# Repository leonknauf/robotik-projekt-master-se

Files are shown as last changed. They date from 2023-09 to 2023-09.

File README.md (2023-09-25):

# D.E.E.Z. N.U.T.S.
**Dynamic Eatables Emitting Zone - Nut Utility Transportation System**

Hier sind alle Projektinformationen sowie die Software für das N.U.T.S Projekt im Rahmen des Moduls Projekt Robotik im Studiengang Systems Engineering von StudiumPlus zu finden.
Anbei einige Bilder, die das Projektergebnis festhalten.
Unter [Releases](https://github.com/leonknauf/robotik-projekt-master-se/releases/tag/release) findet sich außerdem die Präsentation und Dokumentation des Projekt, sowie ein kurzes Werbevideo zu unserem Konzept.

Falls in Zukunft an diesem Projekt weitergearbeitet wird, stehe ich zu Fragen zu dem Projekt oder speziell zu der Software zu Verfügung.

~ Leon Knauf

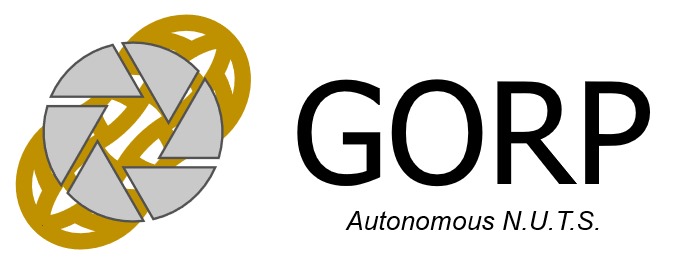
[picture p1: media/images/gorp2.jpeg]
GORP

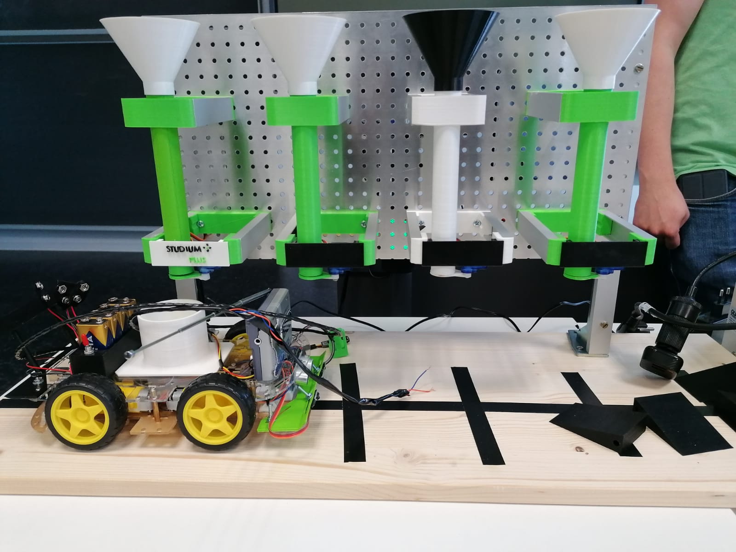
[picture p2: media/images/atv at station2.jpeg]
Vehicle at Station

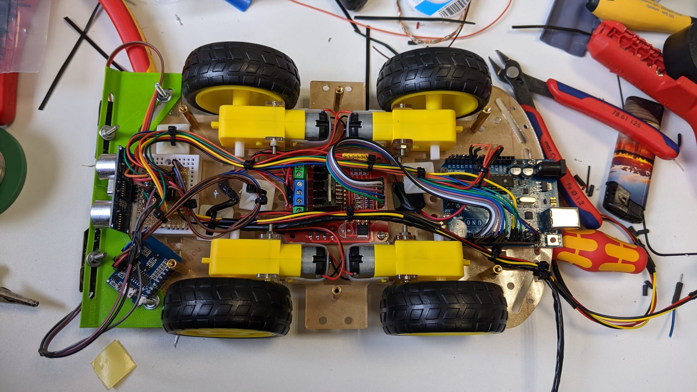
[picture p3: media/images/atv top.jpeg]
Vehicle

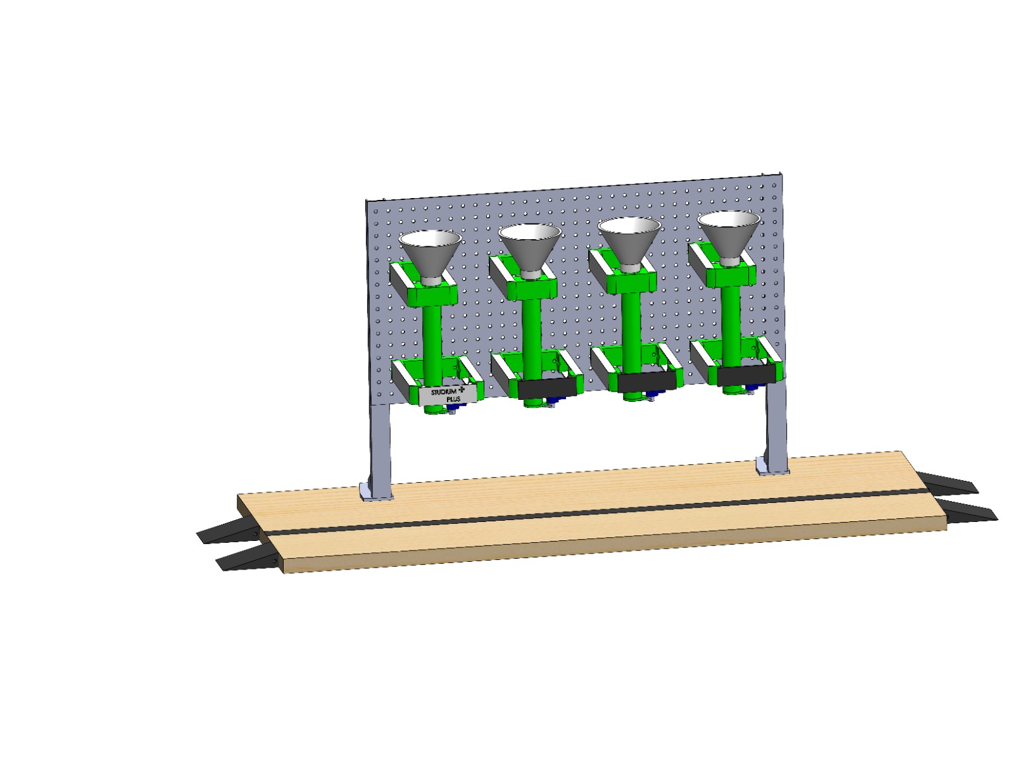
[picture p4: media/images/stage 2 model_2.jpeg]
Station

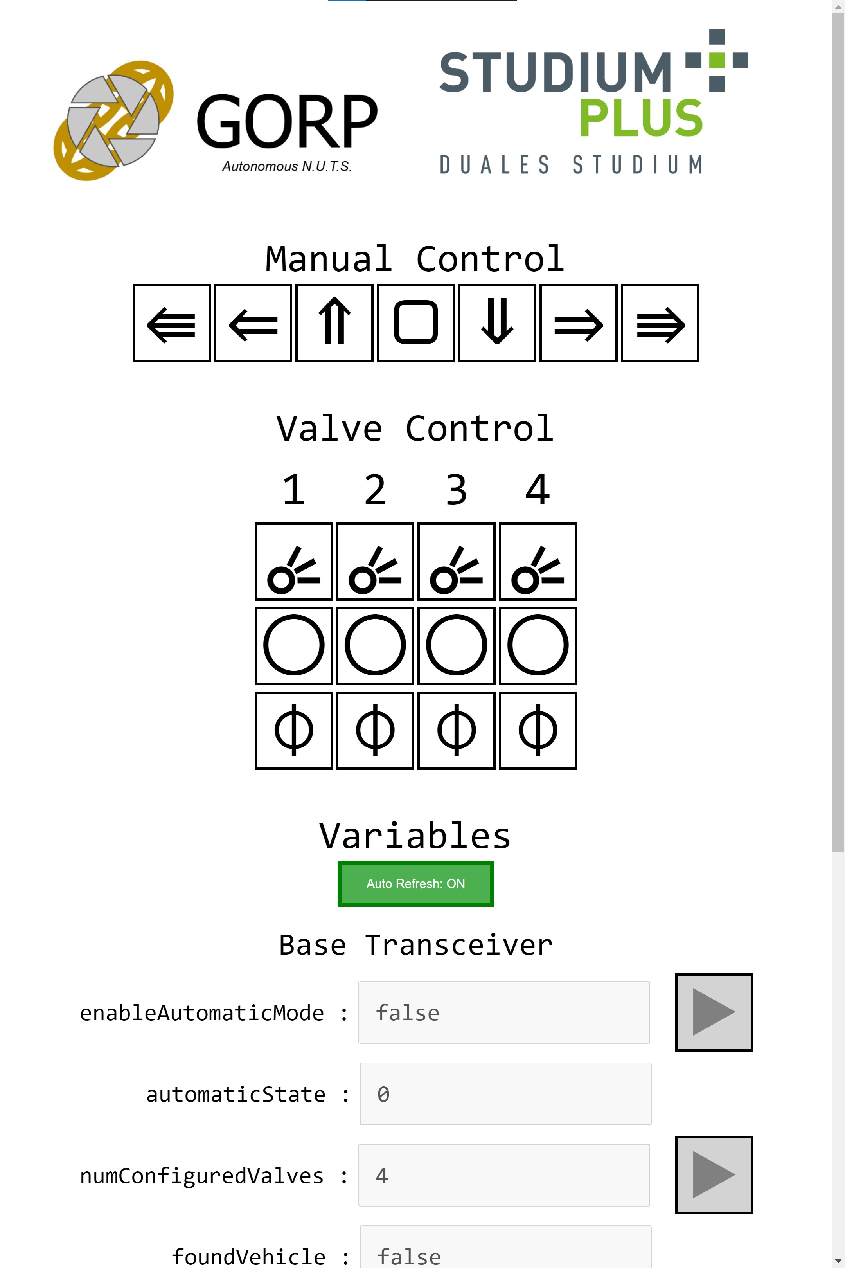
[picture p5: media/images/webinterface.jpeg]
Webinterface


SIEBEL!!!

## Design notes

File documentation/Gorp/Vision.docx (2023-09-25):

# Vision

# Mission Statement

Wir wollen eine Studentenfuttermischmaschine bauen.

Es sollen rohe Nüsse eingefügt und geknackt werden.

Die geknackten Nüsse sollen zusammen mit getrocknetem Obst in eine Tüte verpackt werden.

Optional soll ein AGV die Tüte weitertransportieren.

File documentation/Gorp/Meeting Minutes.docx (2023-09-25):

# Meeting Minutes

# 07.07.2023

- Brainstorming welche Projekte
  - Hauptfokus Nussknacker / Studentenfuttermischmaschine
  - Optional: AGV mit Computer Vision & Path Planning
- Nussknacker
  - Schwungrad, Feder, Rohr
  - hygienisch → Edelstahl

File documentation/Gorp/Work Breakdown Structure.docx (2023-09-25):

# Work Breakdown Structure

- Project Management Activities
  - Process Documentation Activities
    - Setup Communication Channel
      - State: Done
      - Priority: High
      - Assignee: Marvin Müller
      - Planned For: 07.07.2023
      - Completion Date: 07.07.2023
      - Comment: WhatsApp Group set up
    - Setup Documentation Channel
      - State: Done
      - Priority: High
      - Assignee: Marvin Müller
      - Planned For: CW31
      - Completion Date: 04.08.2023
      - Comment: Google Drive folder set up, following documents provided: Vision, Project Plan, Requirement Specification, Test Spec Report, Work Breakdown Structure / Kanban, Meeting Minutes
  - Work Planning Activities
    - Review Meeting with Team Members
      - State: Open
      - Priority: High
      - Assignee:
      - Planned For:
      - Completion Date:
      - Comment:
- Development Activities
  - Mechanical Development Activities
    - Identify Mechanical Components
      - State: Open
      - Priority: High
      - Assignee:
      - Planned For:
      - Completion Date:
      - Comment:
    - Order Mechanical Components
      - State: Open
      - Priority: High
      - Assignee:
      - Planned For:
      - Completion Date:
      - Comment:
    - Assemble Mechanical Components
      - State: Open
      - Priority: High
      - Assignee:
      - Planned For:
      - Completion Date:
      - Comment:
  - Electrical Development Activities
    - Provide Power Supply
      - State: Open
      - Priority: High
      - Assignee:
      - Planned For:
      - Completion Date:
      - Comment:
    - Create AGV
      - State: Open
      - Priority: Low
      - Assignee:
      - Planned For:
      - Completion Date:
      - Comment:
- Test Activities
  - Mechanical Test Activities
    - Nutcracking Tests
      - State: Open
      - Priority: High
      - Assignee:
      - Planned For:
      - Completion Date:
      - Comment:
    - Nutshell Removal Tests
      - State: Open
      - Priority: High
      - Assignee:
      - Planned For:
      - Completion Date:
      - Comment:
  - Electrical Test Activities
    - Power Supply Test
      - State: Open
      - Priority: High
      - Assignee:
      - Planned For:
      - Completion Date:
      - Comment:
    - AGV Test
      - State: Open
      - Priority: Low
      - Assignee:
      - Planned For:
      - Completion Date:
      - Comment:

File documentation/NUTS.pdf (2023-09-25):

Projektbeschreibung Autonomous N.U.T.S | Gorp Group
SE Robotik-Projekt SS23 | Dipl-.Ing. F. Wasinski, Prof. Dr.-Ing. W. Bonath

Projektbeschreibung Autonomous N.U.T.S.

Eingereicht: 24.09.2023

## Inhalt

## Abbildungsverzeichnis

Abb. 1: Gesamtübersicht initiale Planung des N.U.T.S | 4
Abb. 2: High-Level Architektur von Stufe 2 | 5
Abb. 3: Detailed-Level Architektur von Stufe 2 | 5
Abb. 4: High-Level Architektur von Stufe 3 | 6
Abb. 5: Detailed-Level Architektur von Stufe 3 | 6
Abb. 6: High-Level Architektur der Software | 7
Abb. 7: Ansatz von Work Breakdown Structure, Requirements Specification und Test Concept | 7
Abb. 8: CAD-Gesamtansicht der Mechanik von Stufe 2 | 8
Abb. 9: Gesamtansicht der Mechanik von Stufe 3 | 8
Abb. 10: Webseite auf Webserver zur Remote-Kontrolle beider Stufen | 10
Abb. 11: Gesamtansicht des realisierten Teil des N.U.T.S | 11

## 1 Projektplanung

Die Mitglieder des Projekts und deren Hauptarbeitsgebiet waren nach alphabetischer Reihenfolge:

| • Biemer, Felix (Mechanik) • Knauf, Leon (Software) • Kolb, Yannick (Mechanik) • Müller, Marvin (Projektleitung) • Siebel, Jonas (Elektrik) • Zörb, Simon (Elektrik)

Das Team gab sich den Namen „Gorp“, was das englische Wort für „Studentenfutter“ ist. Im

Folgenden ist mit „Gorp Gruppe“ das gesamte Projektteam gemeint. Der verfügbare Zeitraum für das

Projekt war von 07.07.2023 – 24.09.2023. Das verfügbare Projektbudget betrugt 100 – 150 €.

## 2 Projektziel

Das Rahmenthema für das Robotik-Projekt im Studiengang Systems Engineering im Sommersemester

2023 war „Bewegliche autonome Roboter“. Von der Gorp Gruppe wurde dafür mit dem Projekt

„Autonomous N.U.T.S.“ (Nut Utility Transportation System) der Fokus auf die beiden Aspekte gesetzt

| • Nussknackermaschine mit Nussschalentrennung und kontrolliertem Auslassventil • Autonomes Transport-Vehikel (ATV)

Der Gedanke dabei war, eine Studentenfuttermischmaschine zu erstellen, bei der man als Input Nüsse

mit Schale hat und als Output sich sein eigenes Studentenfutter konfigurieren kann.

Für den Nussknackermaschinenteil des N.U.T.S. war der initiale Plan eine Einheit zu erstellen, bei der

Haselnüsse mit Schale erst mittels eines motorbetriebenes Knackmechanismus geknackt werden und

dann mittels Druckluft die Schalen von den Nüssen getrennt werden. Über einen Klappmechanismus

sollten die Nüsse dann ausgegeben werden können.

Der Gedanke hinter der Verwendung eines ATVs war, dass die Hauptanwendung solcher ATVs im

Bereich des autonomen Gütertransportes zu sehen ist [1]. Hierbei gibt zwei Arten von ATVs

| • mit Fahrerkabine, wie z.B. von Torc Robotics [2] oder • ohne Fahrerkabine, wie z.B. von Hyundai [3] oder Volvo [4]

Für das N.U.T.S. sollte ein ATV ohne Fahrerkabine entwickelt werden.

Für eine bessere Planbarkeit wurde das N.U.T.S. in 3 Stages bzw. Stufen unterteilt:

- Stufe 1: Knackmechanismus-Abschnitt der Nussknackermaschine
- Stufe 2: Schalenntrennungs- & Auslass-Abschnitt der Nussknackermaschine
- Stufe 3: ATV

Mit dem N.U.T.S. sollten dabei folgende Ideen des Rahmenthemas besonders fokussiert werden

- Bewegungsalgorithmik – durch die Navigation des ATV
- Selbstorganisation – zwischen der Nussknackermaschine und dem ATV
- Kommunikation zu Systemen untereinander – zwischen der Nussknackermaschine und dem

ATV

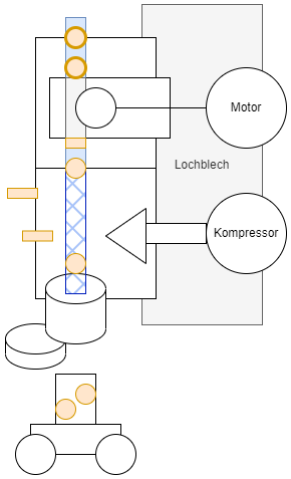
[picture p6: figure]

## 3 Projektumsetzung

Aufgrund von Kostenbeschränkungen (z.B. weil Edelstahl für die Gewährleistung des Hygiene-

Standards bei Lebensmitteln benötigt würde) wurde früh die Stufe 1 als nicht machbar eingeschätzt.

Auch der Schalentrennungsabschnitt wurde aufgrund von Kosten- & Zeitbeschränkungen als nicht

machbar eingeschätzt. Der Hauptfokus im Projekt war folglich auf

| • Stufe 2: Auslass-Abschnitt der Nussknackermaschine • Stufe 3: ATV

Die Haupt-Zielfunktionalitäten wurden dabei festgelegt auf

Abbildung 1: Gesamtübersicht initiale Planung des N.U.T.S.

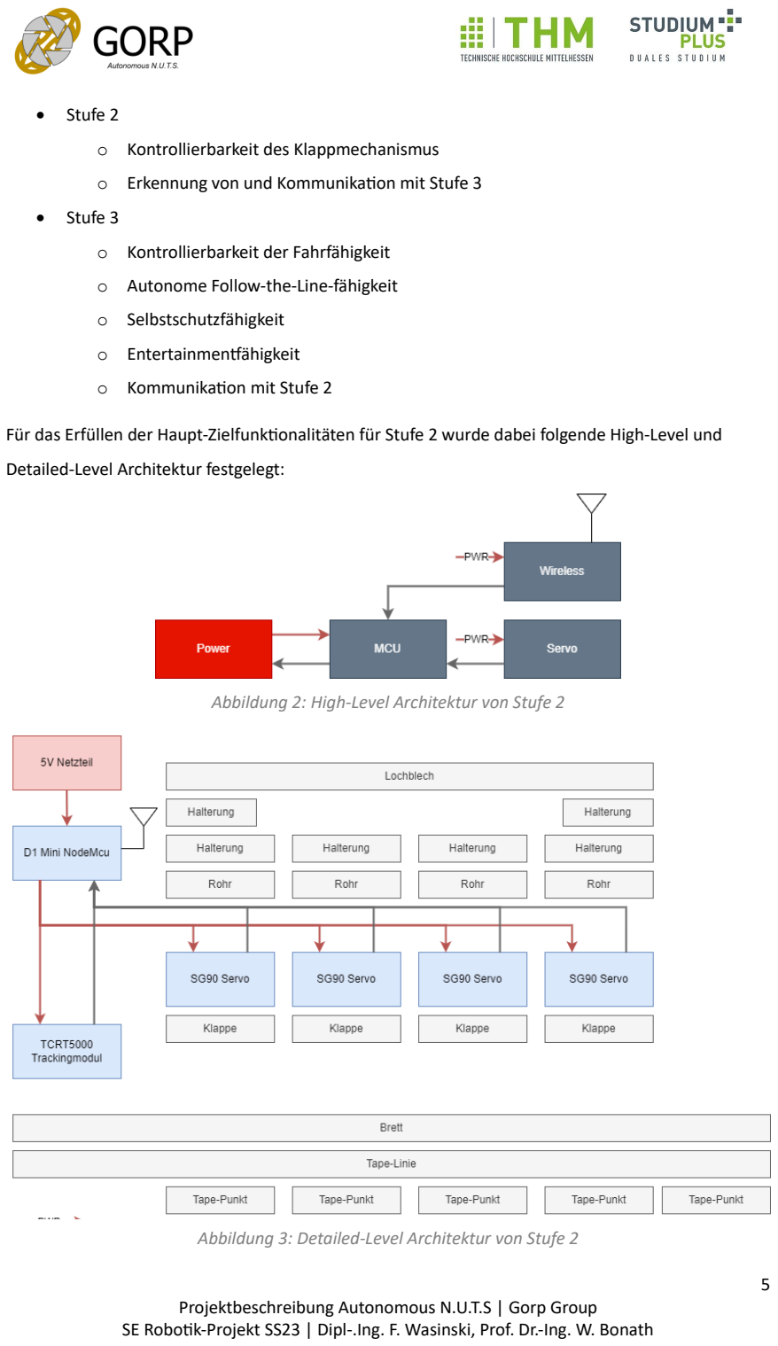
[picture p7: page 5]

- Stufe 2
- Kontrollierbarkeit des Klappmechanismus
- Erkennung von und Kommunikation mit Stufe 3
- Stufe 3
- Kontrollierbarkeit der Fahrfähigkeit
- Autonome Follow-the-Line-fähigkeit
- Selbstschutzfähigkeit
- Entertainmentfähigkeit
- Kommunikation mit Stufe 2

Für das Erfüllen der Haupt-Zielfunktionalitäten für Stufe 2 wurde dabei folgende High-Level und

Detailed-Level Architektur festgelegt:

Abbildung 3: Detailed-Level Architektur von Stufe 2

Abbildung 2: High-Level Architektur von Stufe 2

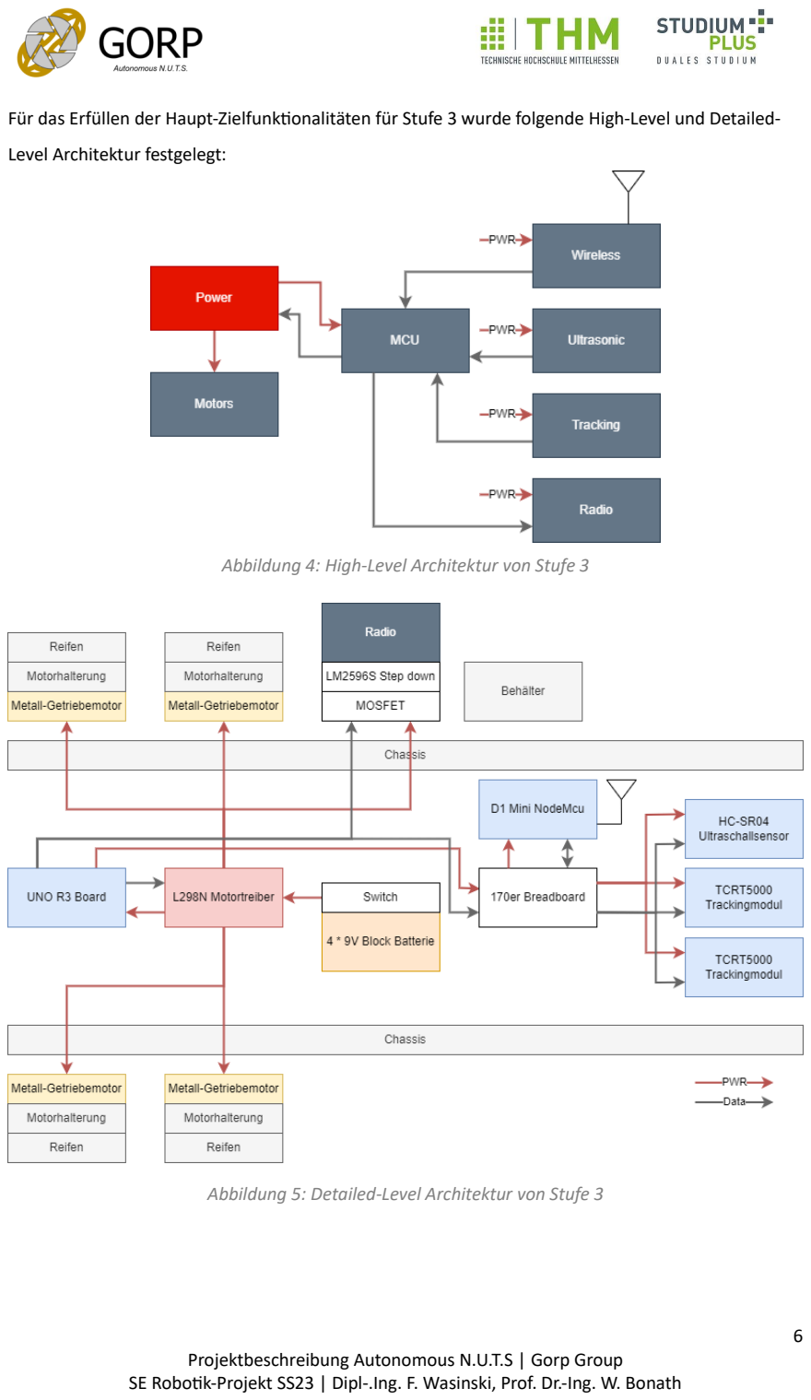
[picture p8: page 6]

Für das Erfüllen der Haupt-Zielfunktionalitäten für Stufe 3 wurde folgende High-Level und Detailed-

Level Architektur festgelegt:

Abbildung 5: Detailed-Level Architektur von Stufe 3

Abbildung 4: High-Level Architektur von Stufe 3

Für die Software wurde folgende High-Level Architektur festgelegt:

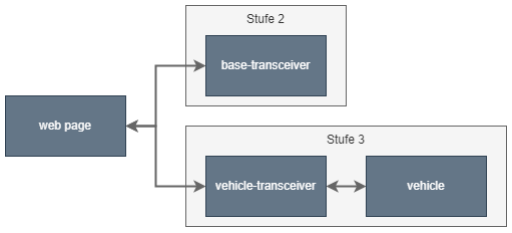
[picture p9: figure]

4 | Erreichter Projektstand
4.1 | System

Auf Systemeben, folgender Stand wurde zum Ende des Projekts erreicht:

- Erstellung von High-Level und Detailed-Level Architekturen.
- Erstellung im Ansatz einer Work Breakdown Structure, einer Requirements Specification und

eines Test Concepts. Aufgrund von Zeitbeschränkungen konnten diese Dokumente nicht

detaillierter ausgeführt werden.

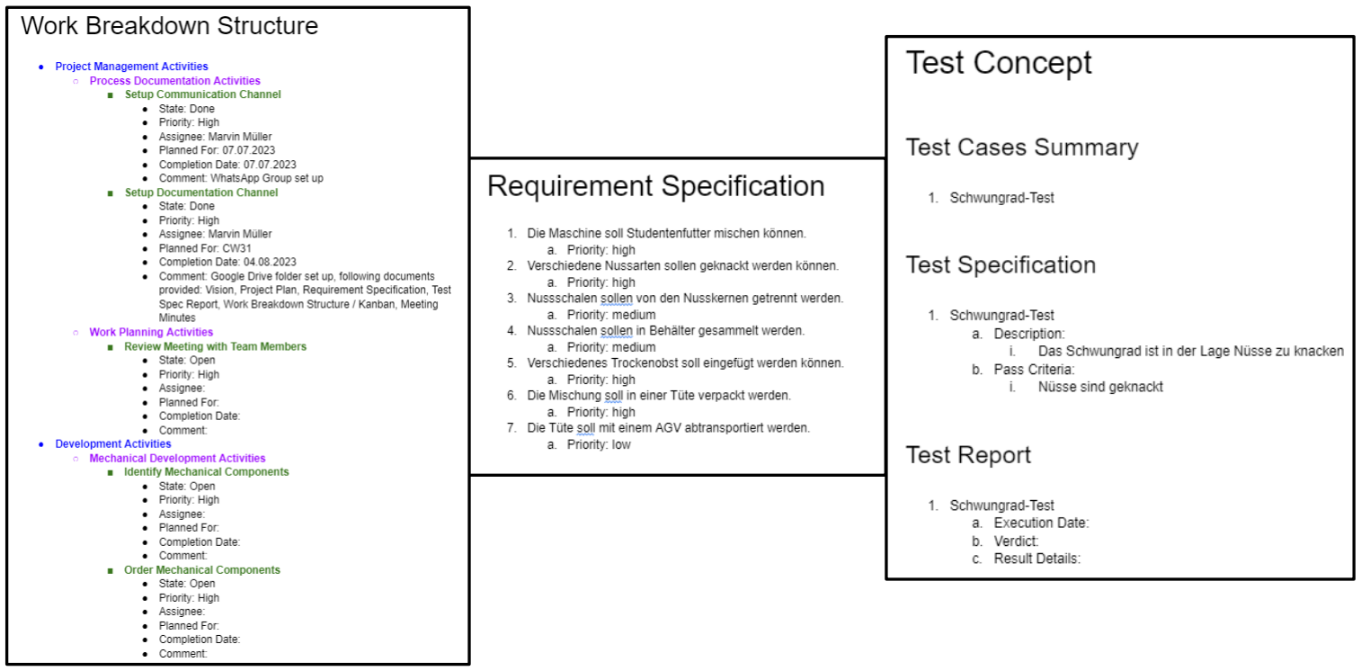
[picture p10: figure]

### 4.2 Hardware

4.2.1 Mechanik

Abbildung 7: Ansatz von Work Breakdown Structure, Requirements Specification und Test Concept

Abbildung 6: High-Level Architektur der Software

Aus mechanischer Sicht wurden für Stufe 2 folgende Punkte realisiert (eine detaillierter Ansicht

befindet sich in Anhang A):

- Erstellung einer Halterung für den Befestigungsmechanismus des Auslassmechanismus
- Erstellung eines Befestigungsmechanismus für den Auslassmechanismus
- 4-malige Erstellung eines Auslassmechanismus bestehend aus Trichter, Rohr und Klappe
- Halterung für den ATV-Erkennungssensor
- Rampen für das ATV

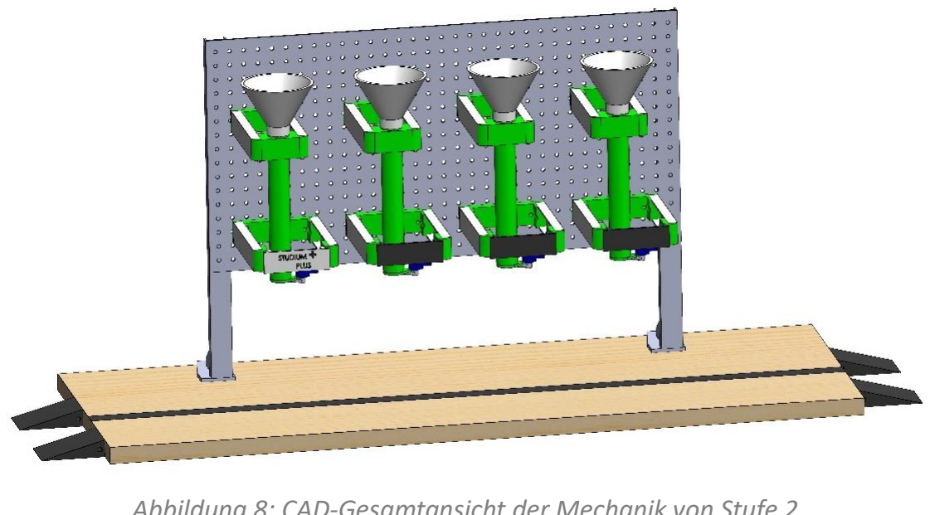
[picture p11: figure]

Für Stufe 3 wurden folgende Punkte realisiert:

- Aufbau des 4WD Smartcar Roboter-Bausatz [5]
- Auffangbehälter
- Front-Schiene für Linienerkennungssensoren

Abbildung 8: CAD-Gesamtansicht der Mechanik von Stufe 2

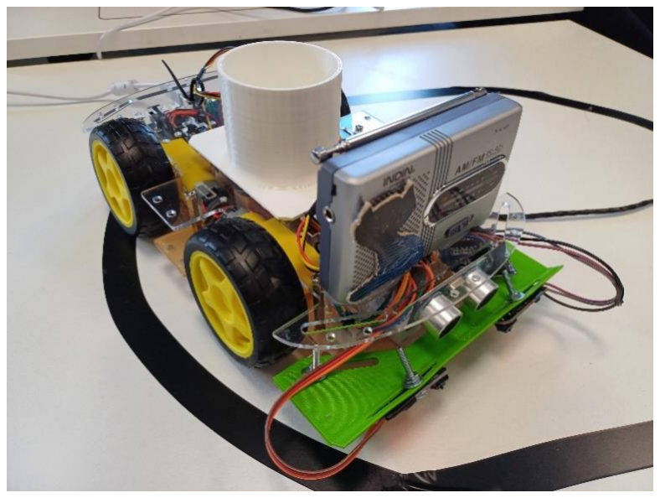
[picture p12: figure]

Abbildung 9: Gesamtansicht der Mechanik von Stufe 3

- Batterieblockhalterung
- Heck-Spoiler

4.2.2 Elektrik

Aus elektrischer Sicht wurden für Stufe 2 folgende Punkte realisiert (eine detaillierter Ansicht

befindet sich in Anhang B):

- 1x Servo SG90 pro Auslassmechanismus
- ATV-Erkennungssensor TCRT5000
- Microcontroller D1 Mini
- 5V Netzteil
- Kabelbaum

Für Stufe 3 wurden folgende Punkte realisiert (eine detaillierter Ansicht befindet sich in Anhang C):

- L298N Motortreiber für 4x Motoren
- Ultraschallsensor HC-SR04
- 2x Follow-the-Line-Sensor TCRT5000
- Microcontroller Arduino Uno
- Microcontroller D1 Mini
- 9V 4x Batterie-Parallelblock
- Radio INDIN BC-R21 Ansteuerung über IRF530NPBF MOSFET und Versorung über LM2596S

Step-Down Converter

- Kabelbaum

### 4.3 Software

Aus Software Sicht wurden für Stufe 2 folgende Punkte realisiert:

- Kontrolle des Klappmechanismus über die Servos SG90
- Bei Auslösen des Sensor TCRT5000 Anweisung gesendet an das ATV in den autonomen

Modus zu wechseln

Für Stufe 3 wurden folgende Punkte realisiert:

- Kontrolle der Richtung und Geschwindigkeit der Motoren
- Kontrolle an/aus des Radios
- Im autonomen Modus Follow-the-Line Fähigkeit mittels der Sensoren TCRT5000

- Im autonomen Modus bei gleichzeitigem Auslösen der Sensoren TCRT5000 Anweisung

gesendet an den Klappmechanismus

- Erstellung eines Webservers mit Webseite zur Remote-Kontrolle und zur Datenübertragung

zwischen den beiden Stufen

Aus Zeitbeschränkungen konnte eine Weiterverarbeitung der Ultraschalldaten nicht realisiert werden.

Detailliertere Sequenz-Diagramme der Detailed-Level Software-Architektur befinden sich in Anhang D

bis F.

Der Source-Code sowie die Rohdateien sämtlicher Blockdiagramme ist in folgendem GitHub-

Repository zu finden: https://github.com/leonknauf/robotik-projekt-master-se/tree/main

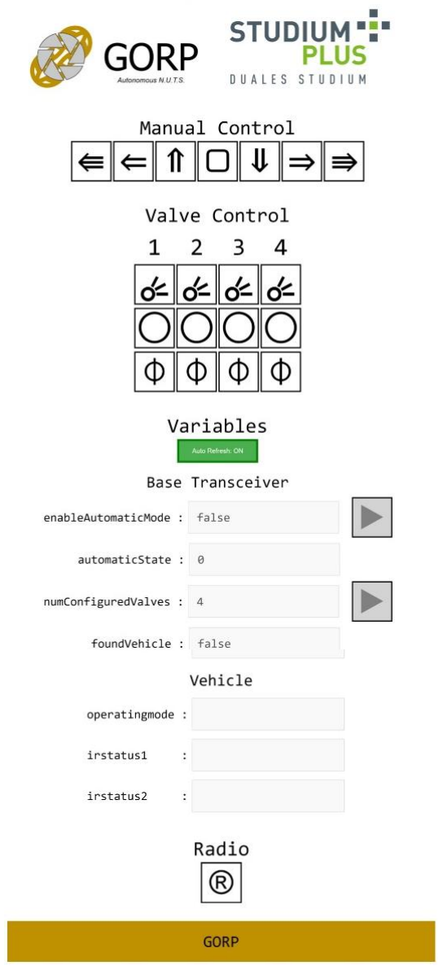
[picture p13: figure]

Abbildung 10: Webseite auf Webserver zur Remote-Kontrolle beider Stufen

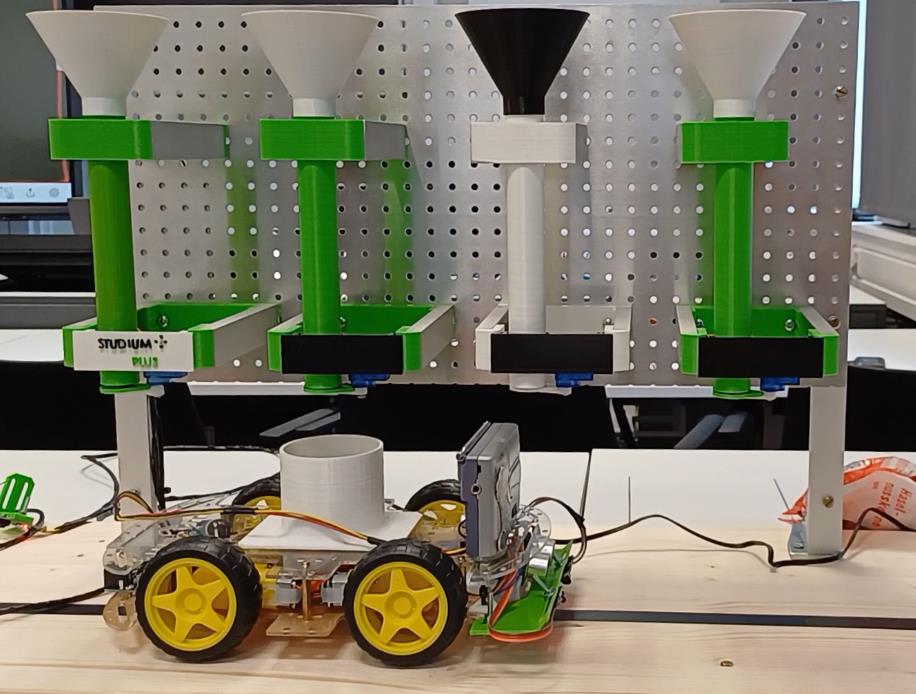
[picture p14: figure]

Abbildung 11: Gesamtansicht des realisierten Teil des N.U.T.S.

## Referenzen

[1] Flämig , Heike, Autonome Fahrzeuge und autonomes Fahren im Bereich des Gütertransportes, in:

Maurer, Markus, Gerdes, J. Christian, Lenz, Barbara, Winner, Hermann (Hrsg.), Autonomes Fahren.

Technische, rechtliche und gesellschaftliche Aspekte, Springer Verlag, S.377-398, 2015

[2] Torc Robotics, Inc., Technology, https://torc.ai/technology/, Abrufdatum 24.09.2023
[3] Hyundai Motor Deutschland GmbH, Hyundai Motor Group stellt Wasserstoff-Vision 2040 vor,

https://www.hyundai.news/de/articles/press-releases/hyundai-motor-group-stellt-wasserstoff-vision-

2040-vor.html, Abrufdatum 24.09.2023

[4] AB Volvo, Vera – Die Zukunft des autonomen Transports, https://www.volvotrucks.de/de-

de/trucks/alternative-antriebe/autonome-lkw/vera.html, Abrufdatum 24.09.2023

[5] anzado GmbH, 4WD Smartcar Roboter-Bausatz, https://www.roboter-bausatz.de/p/4wd-smartcar-

roboter-bausatz, Abrufdatum 24.09.2023

## Anhang

### Anhang A

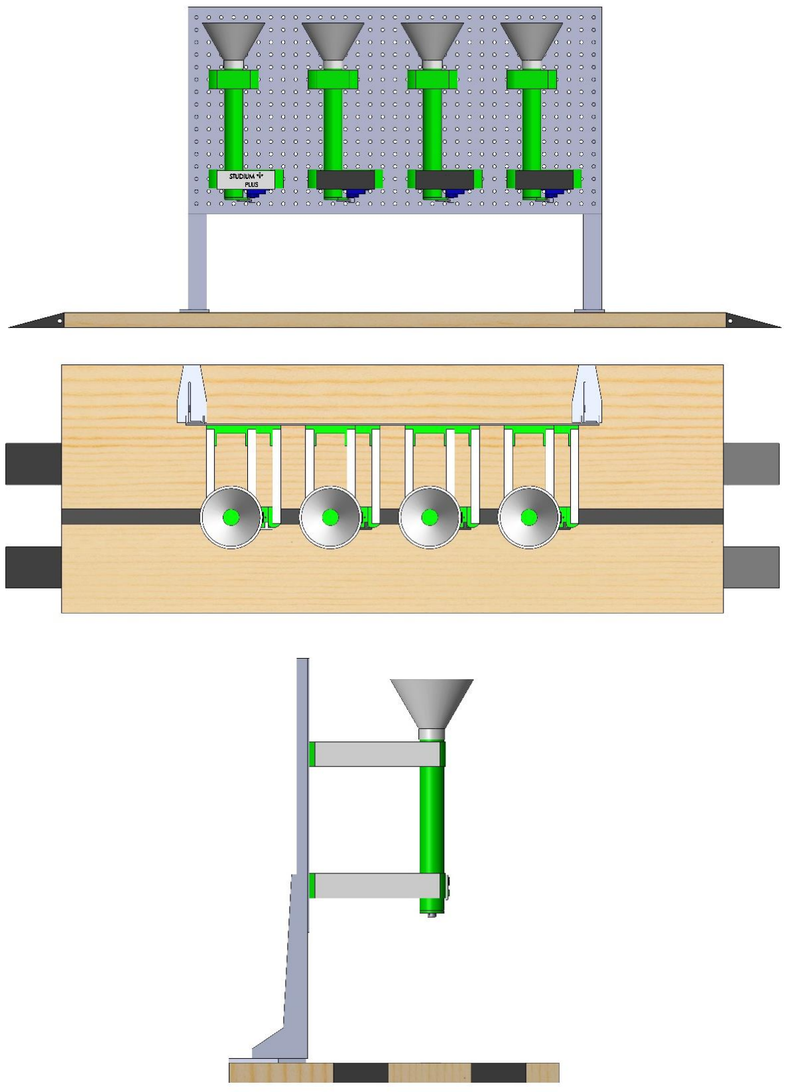
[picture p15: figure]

Anhang A: Front-, Top- & Side-Ansichten der Mechanik von Stufe 2

### Anhang B

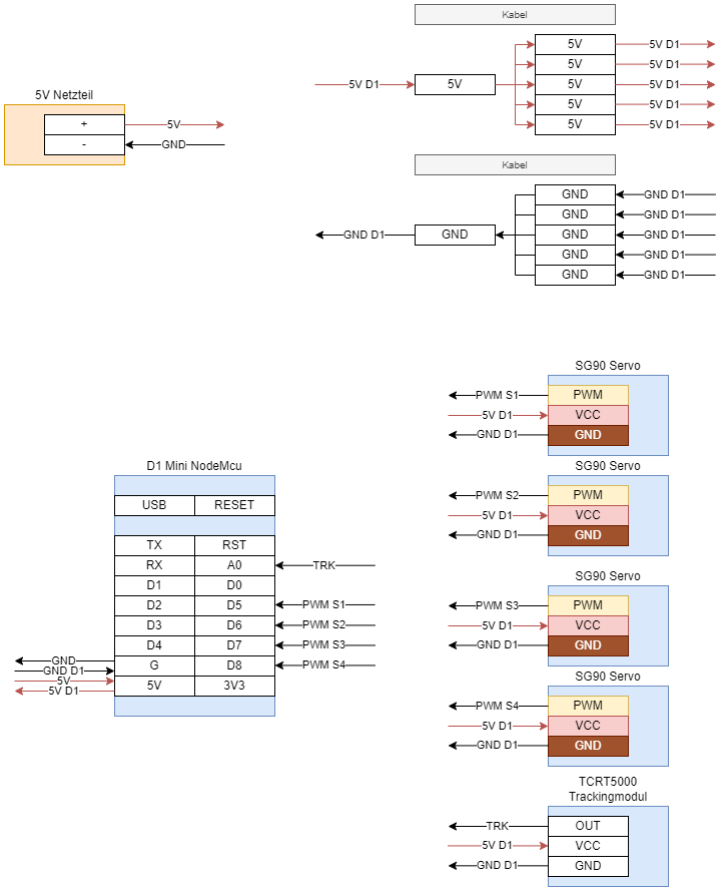
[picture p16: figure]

Anhang B: Elektrischer Schaltplan von Stufe 2

### Anhang C

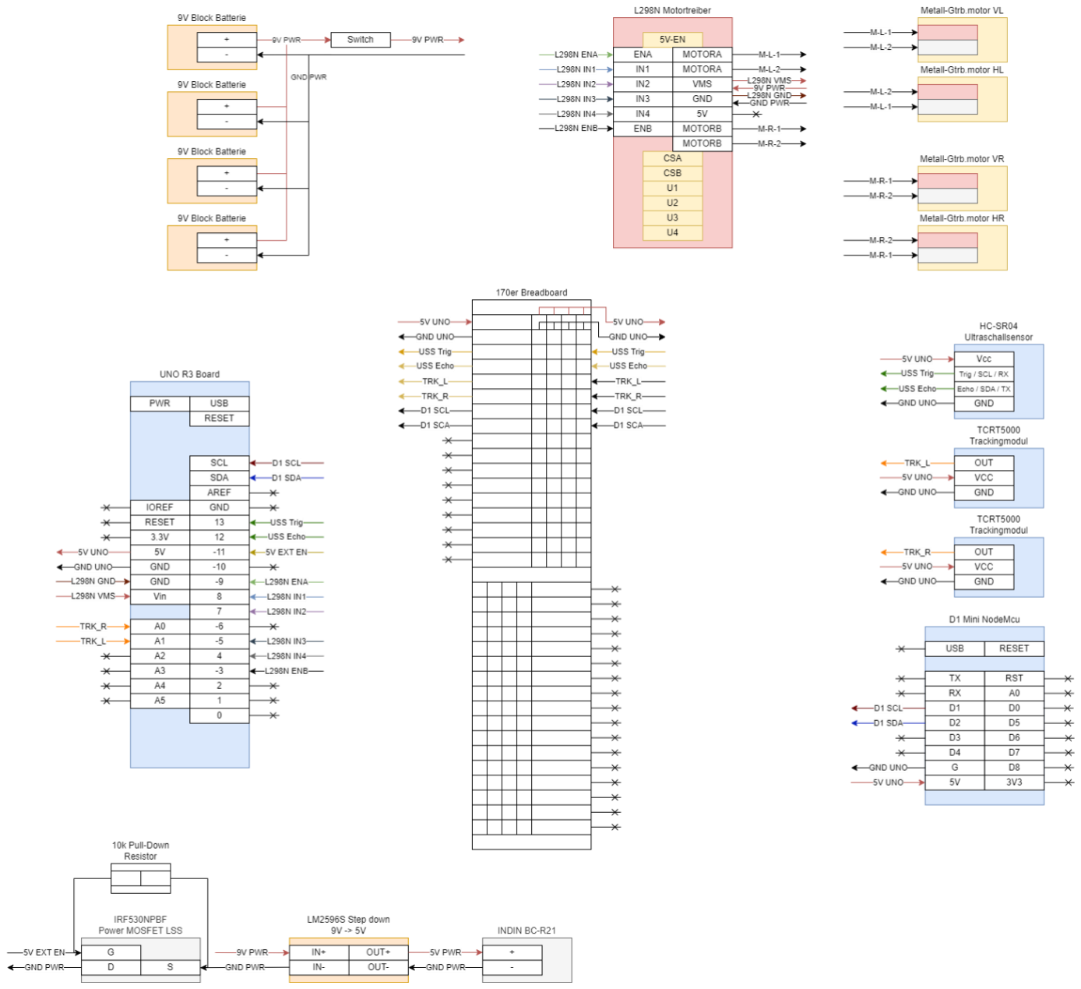
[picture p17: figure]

Anhang C: Elektrischer Schaltplan von Stufe 3

### Anhang D

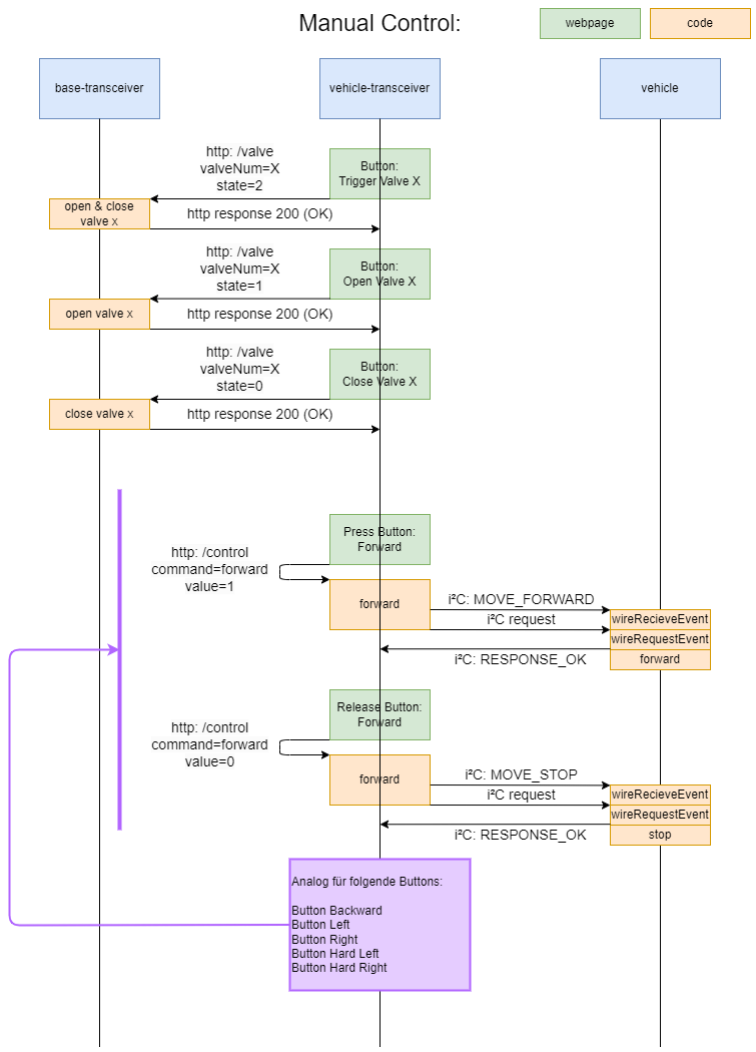
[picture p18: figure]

Anhang D: Sequenzdiagramm von Manual Control

### Anhang E

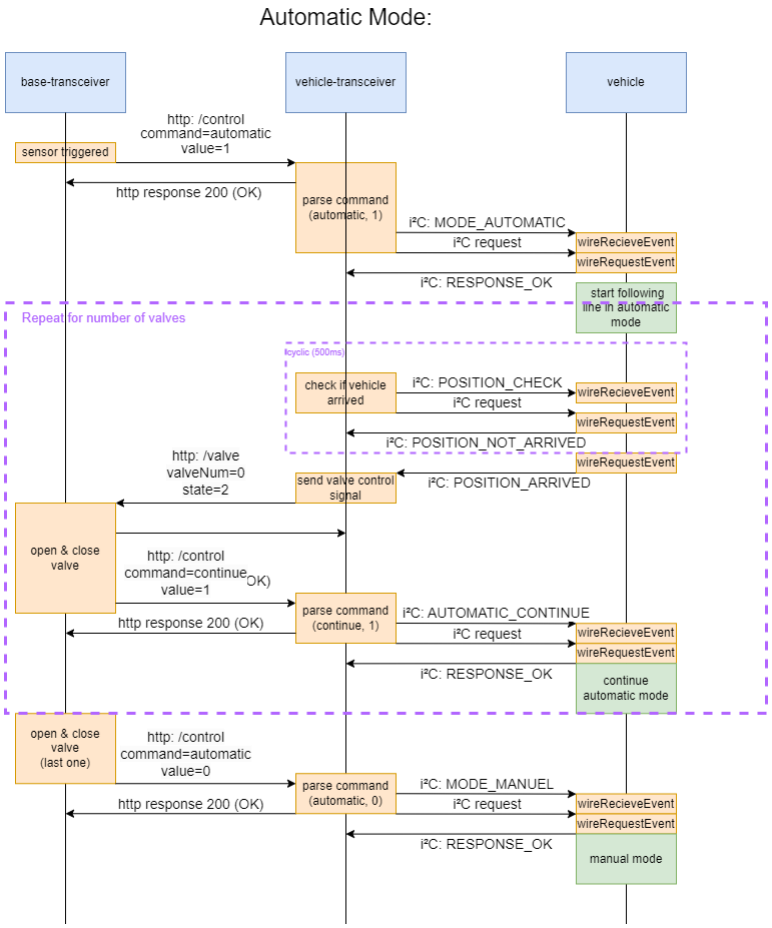
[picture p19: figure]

Anhang E: Sequenzdiagramm von Automatic Mode

### Anhang F

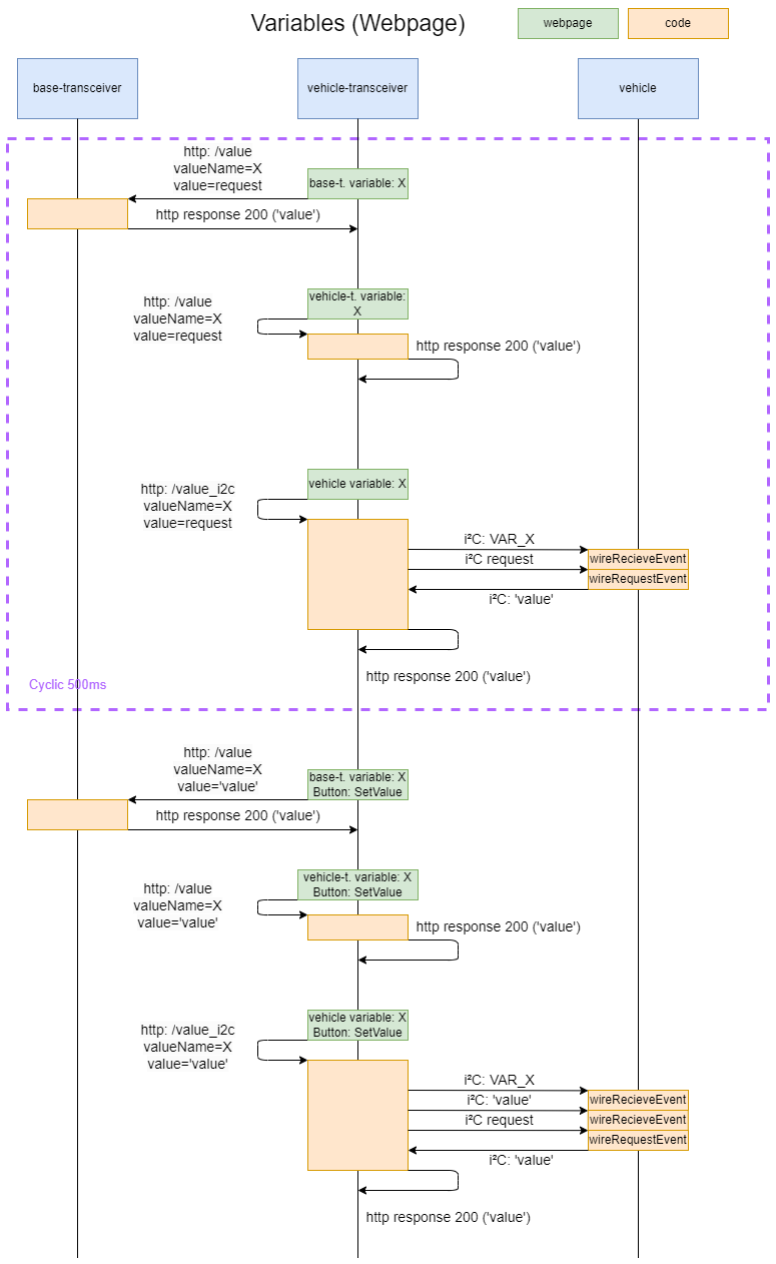
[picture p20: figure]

Anhang F: Sequenzdiagramm von Variables (Webpage)

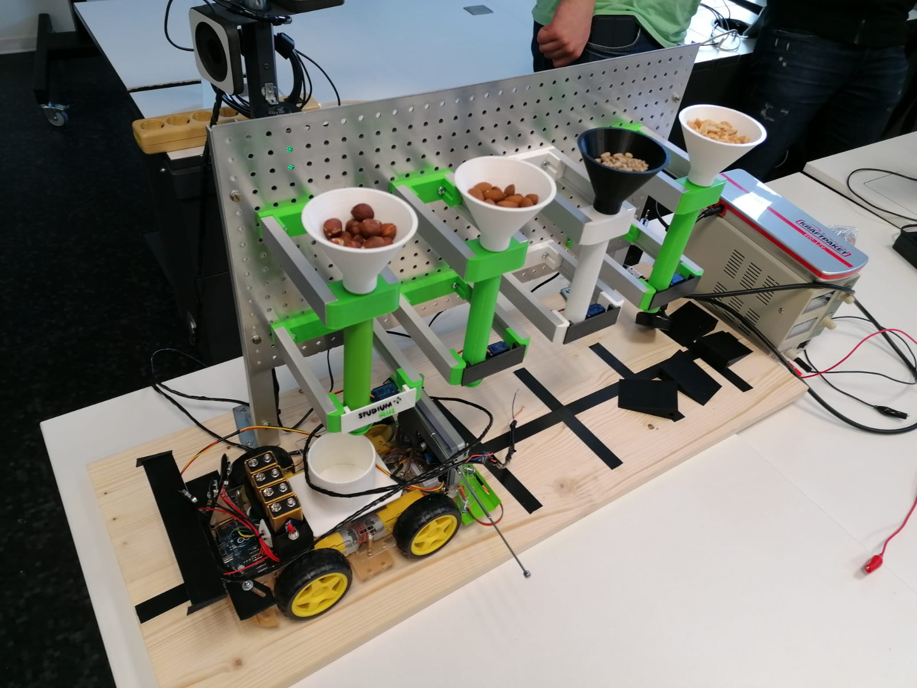
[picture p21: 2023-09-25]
media/images/atv at station1.jpeg

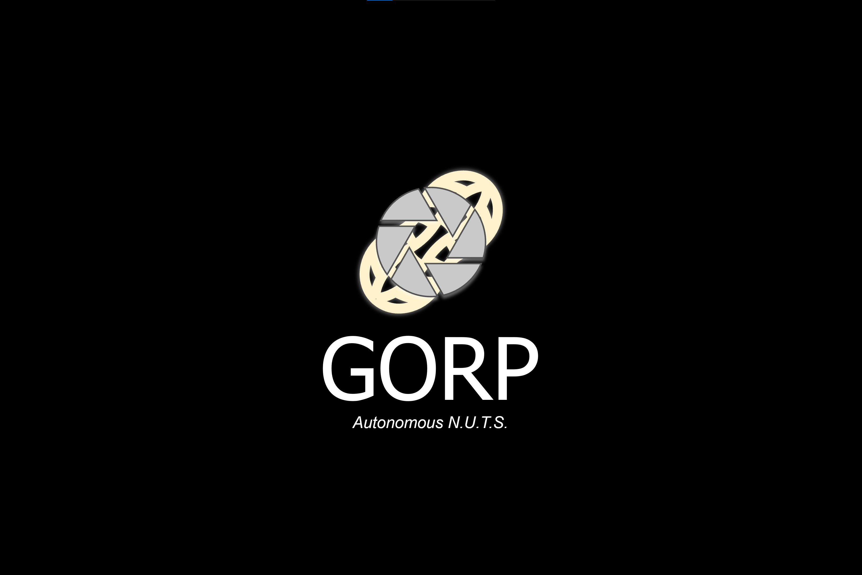
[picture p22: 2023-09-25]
media/images/gorp.jpeg

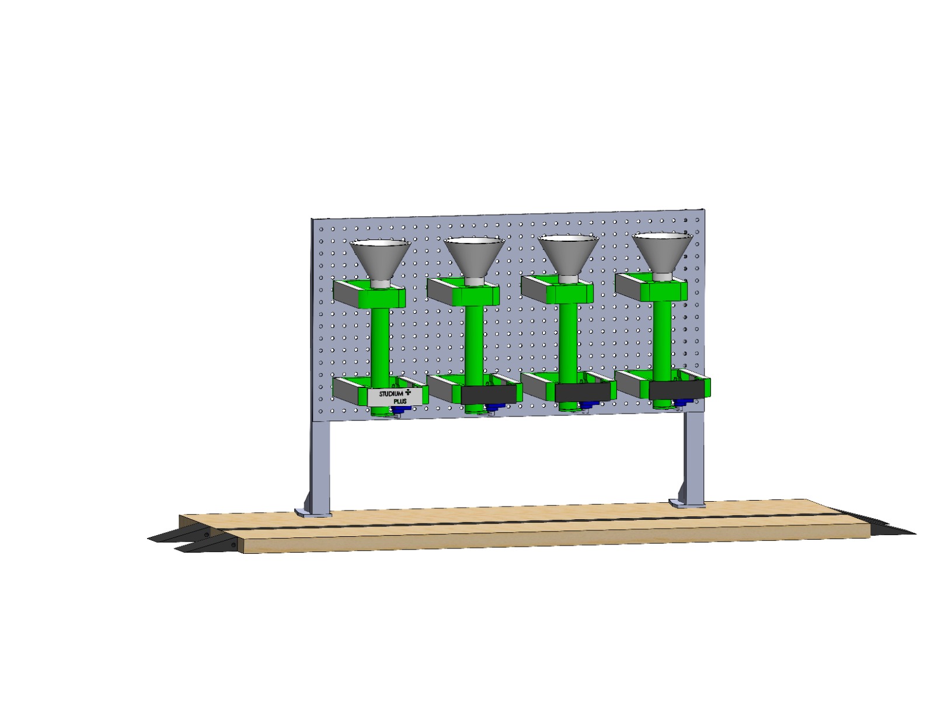
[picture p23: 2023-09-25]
media/images/stage 2 model.jpeg

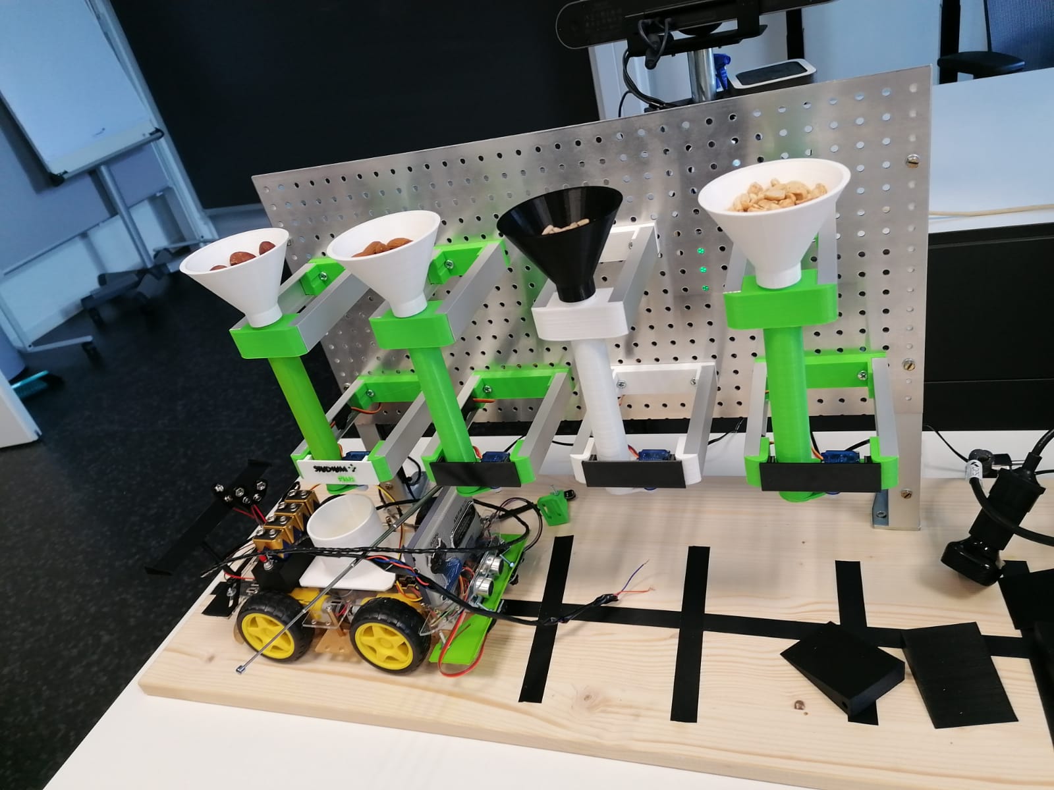
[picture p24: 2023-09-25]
media/images/atv at station3.jpeg

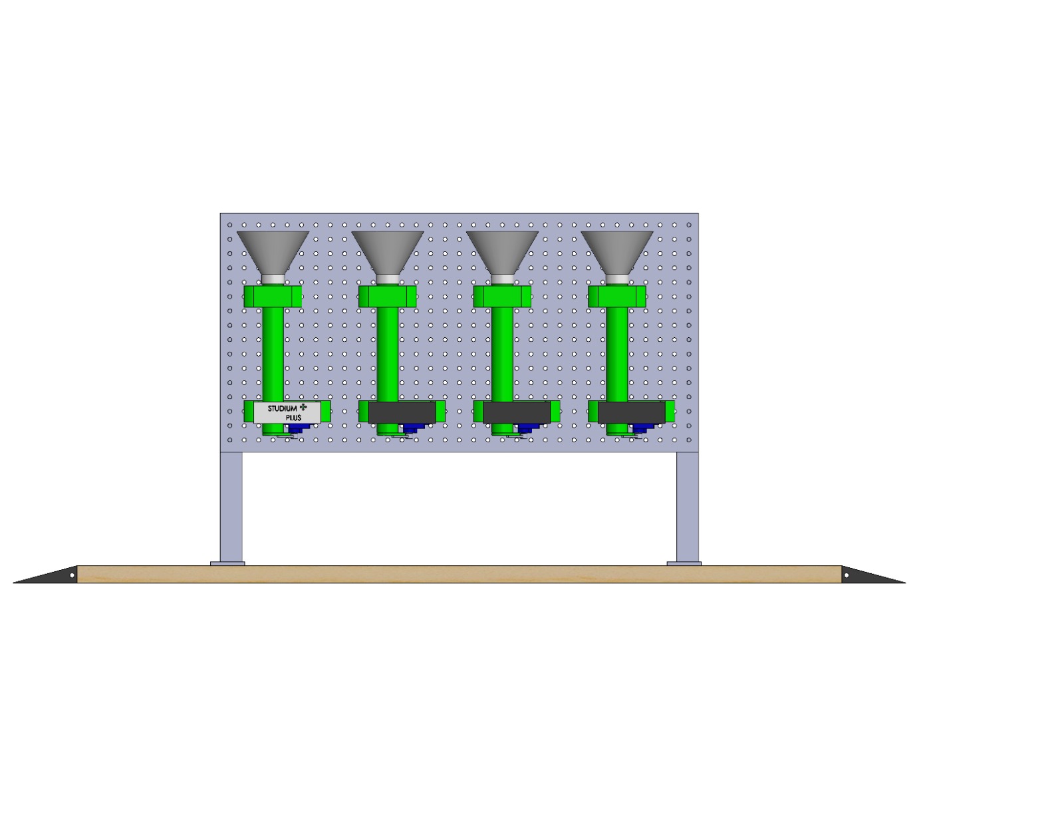
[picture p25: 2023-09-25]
media/images/stage 2 model front.jpeg

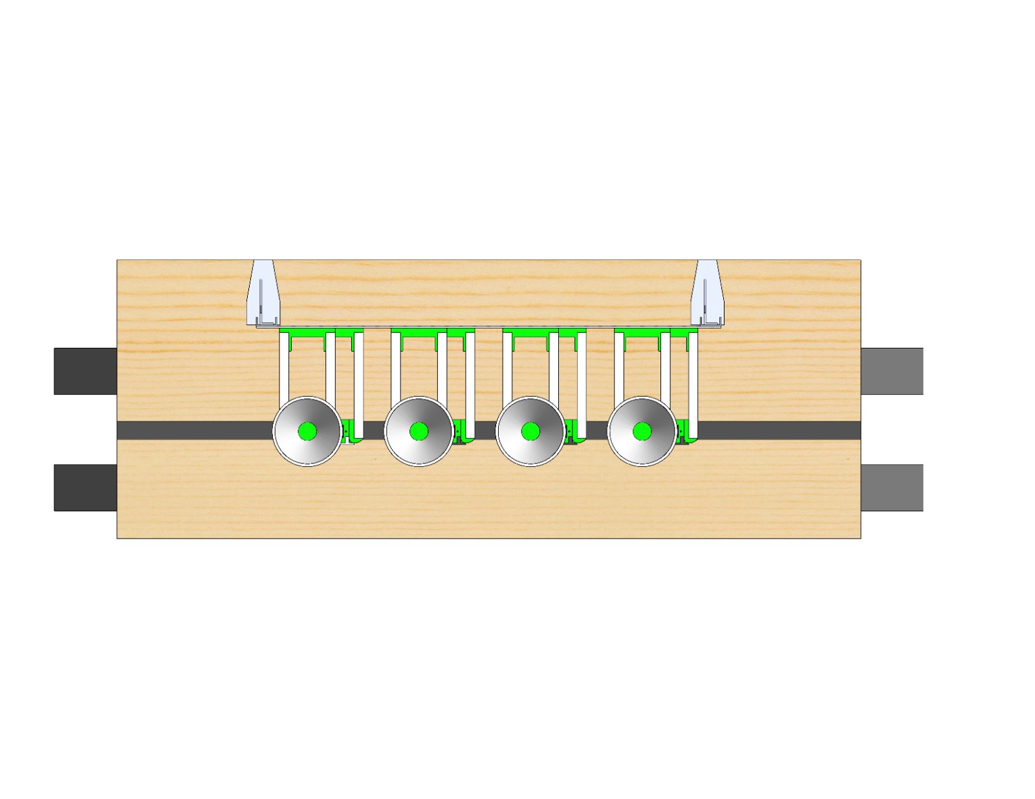
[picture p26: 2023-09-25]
media/images/stage 2 model top.jpeg

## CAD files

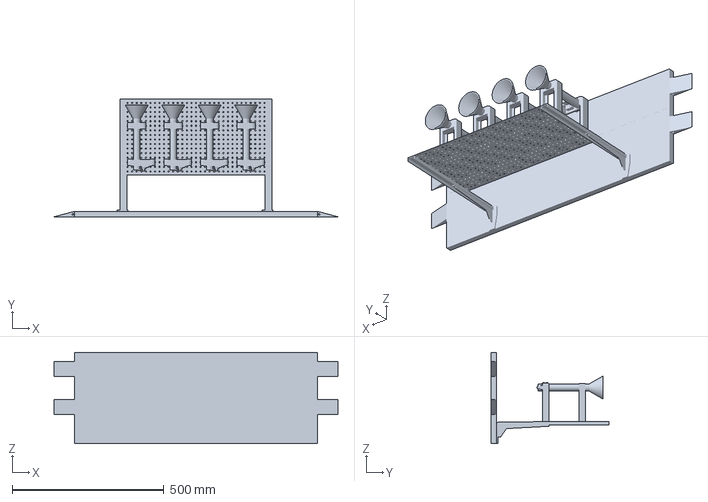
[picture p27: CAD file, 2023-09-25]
media/3d data/Studentenfutterautomat.3MF
934.4 x 387.0 x 300.0 mm

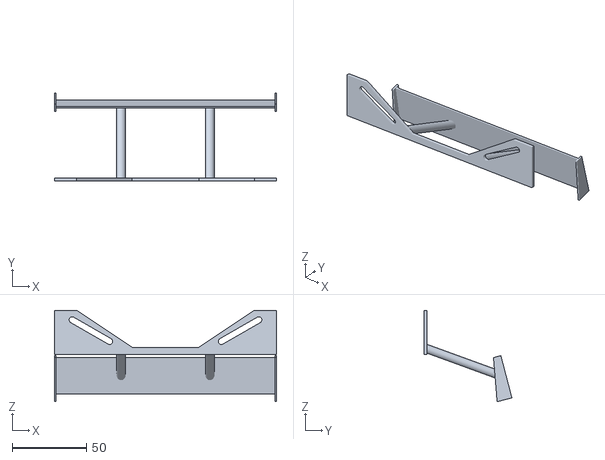
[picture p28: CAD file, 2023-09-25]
media/3d data/Spoiler.STL
150.0 x 59.3 x 61.8

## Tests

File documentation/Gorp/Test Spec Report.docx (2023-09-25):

# Test Concept

# Test Cases Summary

1. Schwungrad-Test

# Test Specification

1. Schwungrad-Test
  a. Description:
    i. Das Schwungrad ist in der Lage Nüsse zu knacken
  b. Pass Criteria:
    i. Nüsse sind geknackt

# Test Report

1. Schwungrad-Test
  a. Execution Date:
  b. Verdict:
  c. Result Details:

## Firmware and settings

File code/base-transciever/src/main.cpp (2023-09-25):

#include <ESP8266WiFi.h>
#include <ESP8266HTTPClient.h>
#include <WiFiClient.h>
#include "ESPAsyncWebServer.h"
#include <String.h>
#include <Servo.h>
#include <ESP8266WiFiMulti.h>

ESP8266WiFiMulti WiFiMulti;

AsyncWebServer server(80);

const char* ssid = "NUTS";
const char* password = "123456789";
IPAddress local_IP(192, 168, 4, 200);
IPAddress gateway(192, 168, 4, 1);
IPAddress subnet(255, 255, 255, 0);

unsigned long previousMillis = 0;
unsigned long readAnalogMillis = 0;
const long interval = 5000; 
int numConfiguredValves = 4;

String test;
String link = "http://192.168.4.1/link1";

#define VALVE1_PIN 15
#define VALVE2_PIN 13
#define VALVE3_PIN 12
#define VALVE4_PIN 14

#define VALVE_POS_CLOSED 0
#define VALVE_POS_OPEN 180

#define VALVE_OPEN_TIME 100 //ms
#define READ_ANALOG_INTERVAL 100

Servo valve1, valve2, valve3, valve4, currentValve;
int currentValveNum;

bool AutomaticValveControl;
bool AutomaticValveControl_mem;

const int TrigSensPin = A0;
bool foundVehicle = false;

bool enableAutomaticMode;
int automaticState = 0;

String httpGETRequest(const char* serverName) {
  WiFiClient client;
  HTTPClient http;
    
  // Your IP address with path or Domain name with URL path 
  http.begin(client, serverName);
  
  // Send HTTP POST request
  int httpResponseCode = http.GET();
  
  String payload = "--"; 
  
  if (httpResponseCode>0) {
    Serial.print("HTTP Response code: ");
    Serial.println(httpResponseCode);
    payload = http.getString();
  }
  else {
    Serial.print("Error code: ");
    Serial.println(httpResponseCode);
  }
  // Free resources
  http.end();

  return payload;
}

void controlValves(String valveNum, String state) {
  int iValveNum = valveNum.toInt();
  int iState = state.toInt();

  if (enableAutomaticMode and (iValveNum > 0 or iState != 2))
    return;

  switch (iValveNum) {
    case 0:
      iValveNum = currentValveNum+1;

    case 1:
      currentValve = valve1;
      break;
    
    case 2:
      currentValve = valve2;
      break;
    
    case 3:
      currentValve = valve3;
      break;

    case 4:
      currentValve = valve4;
      break;

    default:
      Serial.println("Error parsing Command (valveNum)");
      return;
  }
  currentValveNum = iValveNum;

  switch (iState) {
    case 0: //Manual close
      Serial.print("Manual valve control: close valve");
      Serial.println(iValveNum);
      currentValve.write(VALVE_POS_CLOSED);
      break;

    case 1: //Manual open
      Serial.print("Manual valve control: open valve");
      Serial.println(iValveNum);
      currentValve.write(VALVE_POS_OPEN);
      break;

    case 2: //Automatic open and close
      AutomaticValveControl = true;
      break;

    default:
      Serial.println("Error parsing Command (state)");
      return;
  }

}

String readWriteValue(String valueName, String value) {
  if (strcmp(value.c_str(), "request") == 0) {
    //Read value

    if (strcmp(valueName.c_str(), "enableAutomaticMode") == 0)
      return enableAutomaticMode ? "true" : "false";
    else if (strcmp(valueName.c_str(), "automaticState") == 0)
      return String(automaticState);
    else if (strcmp(valueName.c_str(), "numConfiguredValves") == 0)
      return String(numConfiguredValves);
    else if (strcmp(valueName.c_str(), "foundVehicle") == 0) {
      Serial.print("foundVehicle");
      Serial.println(foundVehicle);
      return foundVehicle ? "true" : "false";
    } else
      return "Error";

  } else {
    //Write value

    if (strcmp(valueName.c_str(), "enableAutomaticMode") == 0) {
      if (strcmp(value.c_str(), "true") == 0)
        enableAutomaticMode = true;
      else if (strcmp(value.c_str(), "false") == 0 and automaticState == 0)
        enableAutomaticMode = false;
      return enableAutomaticMode ? "true" : "false";
    } else if (strcmp(valueName.c_str(), "numConfiguredValves") == 0) {
      if (value.toInt() > 0 and value.toInt() <= 4)
        numConfiguredValves = value.toInt();
      return String(numConfiguredValves);
    } else
      return "Error";
  }
}


void setup() {
  Serial.begin(9600);
  Serial.println();

  if (!WiFi.config(local_IP, gateway, subnet)) {
    Serial.println("STA Failed to configure");
  } 
 
  Serial.print("Connecting to ");
  Serial.println(ssid);
  WiFi.begin(ssid, password);
  while (WiFi.status() != WL_CONNECTED) {
    delay(500);
    Serial.print(".");
  }
  Serial.println("");
  Serial.println("Connected to WiFi: "+WiFi.localIP().toString());

  server.on("/valve", HTTP_GET, [](AsyncWebServerRequest *request){
    String valveNum;
    String state;
    // GET input1 value on <ESP_IP>/control?command=<inputMessage1>&value=<inputMessage2>
    if (request->hasParam("valveNum") && request->hasParam("state")) {
      valveNum = request->getParam("valveNum")->value();
      state = request->getParam("state")->value();
    }
    else {
      valveNum = "No message sent";
      state = "No message sent";
    }
    Serial.print("valveNum: ");
    Serial.print(valveNum);
    Serial.print(", Value: ");
    Serial.println(state);
    request->send_P(200, "text/plain", "OK");
    controlValves(valveNum, state);
  });

  server.on("/value", HTTP_GET, [](AsyncWebServerRequest *request){
    String valueName, value;
    // GET input1 value on <ESP_IP>/value?valueName=<inputMessage1>&value=<inputMessage2>
    if (request->hasParam("valueName")) {
      valueName = request->getParam("valueName")->value();
    }
    else {
      valueName = "No message sent";
    }
    if (request->hasParam("value")) {
      value = request->getParam("value")->value();
    }
    else {
      value = "request";
    }

    Serial.print("valueName: ");
    Serial.print(valueName);
    Serial.print(", value: ");
    Serial.println(value);
    
    String response = readWriteValue(valueName, value);
    AsyncWebServerResponse *httpresponse = request->beginResponse(200, "text/plain", response.c_str());
    //Serial.print("response: ");
    //Serial.println(response);
    httpresponse->addHeader("Access-Control-Allow-Headers", "*");
    httpresponse->addHeader("Access-Control-Allow-Origin", "*");
    httpresponse->addHeader("Access-Control-Allow-Methods", "GET, POST, PUT");
    request->send(httpresponse);
  });

  server.begin();

  valve1.attach(VALVE1_PIN, 900, 1500);
  valve1.write(VALVE_POS_CLOSED);
  valve2.attach(VALVE2_PIN, 900, 1500);
  valve2.write(VALVE_POS_CLOSED);
  valve3.attach(VALVE3_PIN, 900, 1500);
  valve3.write(VALVE_POS_CLOSED);
  valve4.attach(VALVE4_PIN, 900, 1500);
  valve4.write(VALVE_POS_CLOSED);

  Serial.println("Setup done");
}

void loop() {
  String response;
  if (millis() - readAnalogMillis >= READ_ANALOG_INTERVAL) {
    foundVehicle = analogRead(TrigSensPin) > 600;
    readAnalogMillis = millis();
  }
  
  
  if (enableAutomaticMode) {
    switch (automaticState) {
      case 0: //wait for vehicle to be in range
        AutomaticValveControl = false;
        currentValveNum = 0;

        if (foundVehicle) { //tell vehicle to follow line
          response = httpGETRequest("http://192.168.4.1/control?command=automatic&value=1");
          Serial.print("Sending automatic=1 request, response: ");
          Serial.println(response);
          automaticState = 10;
        }
        break;

      case 10: 
        if (AutomaticValveControl) {
          Serial.println("Filling vehicle");
          automaticState = 20;
        }
        break;

      case 20:
        if (!AutomaticValveControl) {
          if (currentValveNum >= numConfiguredValves) {
            Serial.println("vehicle filled, done");
            response = httpGETRequest("http://192.168.4.1/control?command=automatic&value=0");
            Serial.print("Sending automatic=0 request, response: ");
            Serial.println(response);
            automaticState = 0;
          } else {
            Serial.println("vehicle filled, continue");
            response = httpGETRequest("http://192.168.4.1/control?command=continue&value=1");
            Serial.print("Sending continue=1 request, response: ");
            Serial.println(response);
            automaticState = 10;
          }
        }
        break;

      default:
        automaticState = 0;
        break;
    } 
  } else {
    automaticState = 0;
  }

  if (AutomaticValveControl) { //Control the current valve
    if (!AutomaticValveControl_mem) {
      Serial.print("Automatic valve control: open valve");
      Serial.println(currentValveNum);
      currentValve.write(VALVE_POS_OPEN);
      previousMillis = millis();
      AutomaticValveControl_mem = true;
    } else {
      if (millis() - previousMillis >= VALVE_OPEN_TIME) {
          Serial.print("Automatic valve control: close valve");
          Serial.println(currentValveNum);
          currentValve.write(VALVE_POS_CLOSED);   
          AutomaticValveControl = false;
          AutomaticValveControl_mem = false; 
      }
    }
  } 
}

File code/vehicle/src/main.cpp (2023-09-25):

/*
 *Filename: Code Arduino N.U.T. 
 *Author: Jonas Siebel
 *Date:22.09.2023
 *Version: 1.1
 *
 *Password for NUTS-WIFI: 
 *123456789
 *
 *Web-Adress for remote controll:
 *192.168.4.1
*/


/*
UnschÃ¶n:
1) Es gibt globale variablen
2) Die Funktion die bei einem I2C INterrupt aufgerufen wird ist zu lang
   Vielleicht mit Markern arbeiten und einen Teil davon ins Hauptprogramm verschieben?
*/


//==================================libs=============================

#include <Servo.h>    //servo motor lib
#include <HCSR04.h>   //ultrasonic lib
#include <Wire.h>     //I2C lib

//==================================pins==============================

//pins motor a
int enA = 9;
int in1 = 8;
int in2 = 7;

//pins motor b
int enB = 3;
int in3 = 5;
int in4 = 4;

//pins ultrasonic sensor
const int trigPin = 13;
const int echoPin = 12;
UltraSonicDistanceSensor distanceSensor(trigPin, echoPin);

//pins IR-Sensors
const int irsenspin1 = A1;
const int irsenspin2 = A0;

//pins Radio
const int radiopin = 11;


//=================================global variables==============================

bool operatingmode = true;      //true -> remote controlled, false -> line following
bool inposition = false;        //NUT in position under dispenser in line following mode?
bool automatic_continue = true; //station finished filling, vehicle can start again

int i2c_response;

//local for main() only
bool irstatus1 = 0;
bool irstatus2 = 0;

//speeds for driving curves and driving forward*
int curvespeed = 150;
int forwardspeed = 100;
//*they have to be different, because driving a curve requires more power aka speed


//===============================enumerations for I2C================================
enum i2cCommand{
  UNDEFINED,
  RESPONSE_OK,
  MOVE_STOP,
  MOVE_FORWARD,
  MOVE_BACKWARD,
  MOVE_LEFT,
  MOVE_RIGHT,
  MOVE_HARD_LEFT,
  MOVE_HARD_RIGHT,
  MODE_AUTOMATIC, //activate line following mode
  MODE_MANUEL,    //activate remote controlled driving mode
  POSITION_CHECK,   //in position?
  POSITION_ARRIVED, //yes, in position
  POSITION_NOT_ARRIVED, //no, not in position
  AUTOMATIC_CONTINUE, //switch back in remote controlled mode
  VAR_IRSTATUS1,  //status ir sensor 1
  VAR_IRSTATUS2,  //status ir sensor 2
  VAR_OPMODE, //status operation mode
  RADIO_ON,
  RADIO_OFF
};


//==================================functions====================================

//set speed of all motors on a value between 0 and 255 (min. 100 recommended)
void set_speed(int velocity){
  analogWrite(enA, velocity);
  analogWrite(enB, velocity);
}

//stop the movement
  void move_stop(){
    digitalWrite(in1, LOW);
    digitalWrite(in2, LOW);
    digitalWrite(in3, LOW);
    digitalWrite(in4, LOW);
  }

//drive forward
  void move_for(){
    set_speed(forwardspeed); 
    digitalWrite(in1, HIGH);
    digitalWrite(in2, LOW);
    digitalWrite(in3, HIGH);
    digitalWrite(in4, LOW);
  }

//drive backward
  void move_back(){
    set_speed(forwardspeed); 
    digitalWrite(in1, LOW);
    digitalWrite(in2, HIGH);
    digitalWrite(in3, LOW);
    digitalWrite(in4, HIGH);
  } 

//drive sharp to the right
  void move_sright(){
    set_speed(curvespeed); 
    digitalWrite(in1, HIGH);
    digitalWrite(in2, LOW);
    digitalWrite(in3, LOW);
    digitalWrite(in4, HIGH);
  }

//drive sharp to the left
  void move_sleft(){
    set_speed(curvespeed); 
    digitalWrite(in1, LOW);
    digitalWrite(in2, HIGH);
    digitalWrite(in3, HIGH);
    digitalWrite(in4, LOW);
  } 

//drive to the right
  void move_right(){
    set_speed(curvespeed); 
    digitalWrite(in1, HIGH);
    digitalWrite(in2, LOW);
    digitalWrite(in3, LOW);
    digitalWrite(in4, LOW);
  }

//drive to the left
  void move_left(){
    set_speed(curvespeed); 
    digitalWrite(in1, LOW);
    digitalWrite(in2, LOW);
    digitalWrite(in3, HIGH);
    digitalWrite(in4, LOW);
  } 

//=========

//switch radio on/off
  void radio_on(){
    digitalWrite(radiopin, HIGH);
  }

  void radio_off(){
    digitalWrite(radiopin, LOW);
  }

//=======

//communication with esp via I2C (triggerd by an I2C interrupt)
void wireReceiveEvent(int bytes){
  int recieved_command = Wire.read();   //store recieved command
  i2c_response = RESPONSE_OK; 

  Serial.print("i2C Recieved: ");
  Serial.println(recieved_command);

  //interrupts which always work
  switch(recieved_command){
    case VAR_IRSTATUS1:
    i2c_response = irstatus1;
    break;
    
    case VAR_IRSTATUS2:
    i2c_response = irstatus2;
    break;
    
    case VAR_OPMODE:
    i2c_response = operatingmode;
    break;
    
    case RADIO_ON:
    radio_on();
    break;
    
    case RADIO_OFF:
    radio_off();
    break;
  }
   

  //remote controlled driving interrupts
  if(operatingmode == 1){
    switch(recieved_command){
      case MOVE_STOP:
      move_stop();
      break;
  
      case MOVE_FORWARD:
      move_for();
      break;
  
      case MOVE_BACKWARD:
      move_back();
      break;
  
      case MOVE_LEFT:
      move_left();
      break;
  
      case MOVE_RIGHT:
      move_right();
      break;
  
      case MOVE_HARD_LEFT:
      move_sleft();
      break;
  
      case MOVE_HARD_RIGHT:
      move_sright();
      break;

      //switch to line following mode
      case MODE_AUTOMATIC:
      operatingmode = 0;
      break;
    }
  } 
  
  //line following mode interrupts
  else if(operatingmode == 0){
    switch (recieved_command){    
      case POSITION_CHECK://are you in position?
        if(inposition == true){
          i2c_response = POSITION_ARRIVED; //yes, in position
          inposition = false;
        }
        else{
          i2c_response = POSITION_NOT_ARRIVED; //no, not in position
        }
        break;

      //switch to rc driving mode
      case MODE_MANUEL:
        operatingmode = 1;
        break;

      //station complete, continue
      case AUTOMATIC_CONTINUE:
        automatic_continue = true;
        break;
    }
  }
}

//=======
  
void wireRequestEvent(){
  Serial.print("i2C Request, answering: ");
  Serial.println(i2c_response);
  Wire.write(i2c_response);
  i2c_response = RESPONSE_OK;
}

//=========================================setup================================

void setup()
{
  //Set all the motor control pins to outputs
  pinMode(enA, OUTPUT);
  pinMode(enB, OUTPUT);
  pinMode(in1, OUTPUT);
  pinMode(in2, OUTPUT);
  pinMode(in3, OUTPUT);
  pinMode(in4, OUTPUT);

  pinMode(radiopin, OUTPUT);

  Serial.begin(9600); //start debug

  Wire.begin(1);  //start I2C
  Wire.onReceive(wireReceiveEvent); //interrupt through I2C on
  Wire.onRequest(wireRequestEvent);
}
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

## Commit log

2023-09-08 vehicle transciever webserver & i2c communication
2023-09-08 vehicle i2c communication
2023-09-09 Stage3 Schematic
2023-09-09 base-transciever valve control
2023-09-09 vehicle rework from j. siebel
    [main.cpp]
2023-09-14 fixed i2c communication
2023-09-18 reworked communication and automatic procedure
    [main.cpp]
2023-09-20 Used enum for the i2c communication (why didn't i think of this before?)
    [main.cpp]
2023-09-22 button css
2023-09-25 media files
    [Spoiler.STL, Studentenfutterautomat.3MF]
